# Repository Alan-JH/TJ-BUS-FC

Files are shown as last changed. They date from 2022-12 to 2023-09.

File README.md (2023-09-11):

# Piridium Hardware
Piridium is a CubeSat bus design inspired by TJREVERB and the concept of Pycubed. It uses a Raspberry Pi Zero as a flight computer and Iridium 9602N modem as a radio. The bus is divided into two boards, with the EPS board including six 18650 battery cells and protection and balancing circuitry, and the avionics board including everything else (flight computer, radio, telemetry ADC, inhibits and RBF, solar input charge regulators, 5V output regulator, inertial measurement unit, real time clock and CR2032 battery backup, and payload connector).

## Issues
Charge balance for current EPS prototype seems to not work, despite following datasheet recommendations exactly. Possibly a bad chip, but worth noting.

## Tech Specs
Flight Computer: Raspberry Pi Zero/Zero W

Radio: Iridium 9602N Short Burst Data

Clock: DS3232M RTC with CR2032 Battery Backup

Battery: Six 18650 Li-Ion cells (builder's discretion, recommend protected 3-4Ah) in a 3P2S configuration

Battery protection: ~7.7A overcurrent protection (charge & discharge), 4.29V/cell overcharge protection with hysteresis down to 4.05V/cell, 3V/cell overdischarge protection with hysteresis up to 3.2V/cell

Solar input: 4 input connectors feeding two regulators with 25V Max (limited by the voltage divider for telemetry) with charge cutoff at 8.27V, MPPT settable using a trim pot

Output regulation: 2 separated 5V rails up to 3A output, one for the radio, the other for the Raspberry Pi, each with latching current limiters and a watchdog timer

Payload connection: 1x SPI bus with one dedicated chip enable pin, 1x I2C bus, 1x unused configurable GPIO pin, switchable battery power (no overcurrent protection); see schematic for pinout

Telemetry: Current out and voltage in for both solar regulators, battery input voltage and current, payload battery current

Antenna connector: Standard SMA vertical

Inhibits: Two discharge inhibits (do not block charge), two RBF (one low side ground disconnect, one high side power disconnect, blocks both charge and discharge)

## Hardware notes

### Flight Computer
Raspberry Pi Zero running Raspbian OS lite. Flight software can be found here: https://github.com/Alan-JH/piridium-fsw

### Iridium Modem
Defaults to off when the bus is powered, only turns on when S_MODEM_ON_OFF is pulled high by the Raspberry Pi on GPIO pin 20. There is an LED to indicate when the modem is powered, and GPIO input for ring indicator and network availability (S_RING_INDICATOR on GPIO pin 16 and S_NET_AVAIL on GPIO pin 12, respectively). Communication with the device is done through 3.3V UART, connected to the single UART bus on the Raspberry Pi. There is also a separate connector on the board to be used with a USB to UART converter in case configuration is needed without access to the Raspberry Pi. Due to its strict power requirements the modem can only be powered with the avionics board's 5V regulators, and not through the extra port. All UART connections driven by the Pi run through a 74HC126 buffer to the modem, to prevent latchup conditions if the modem is powered off. A separate patch antenna is required, and can connect with the SMA connector on the board.

### Power Input
There are two LT3652 MPPT tracking charge regulators on the board, each with two input connectors in parallel. The intent is for two solar panels on opposite sides of the CubeSat to be connected to the input of the same regulator, since one will not be producing power while the other is. Input voltage can range up to 25V, and the maximum power point can be set using the trim potentiometer on each regulator. I recommend doing this by connecting a power supply to the input connector, setting its voltage to the desired maximum power point voltage (Vmpp) and adjusting the trim pot until the voltage at the Vmpp test point is 2.7V. The regulators each output up to 2A, and cut off charge at 8.27V float and 0.2A termination. 

### 5V Regulator
There is one TPS54394RSAR regulator on board which outputs two isolated 3A buses, which are configured to 5V. One (labelled 5VP in the schematic) feeds the radio and must not be shared with anything else. The other (labelled 5V in the schematic) feeds the RPi and may be shared, although there is no connector native to the board to do this (and it isn't recommended to share it anyways, as the RPi is an important component). Each rail has its own 5V latching current limiter that disconnects its respective voltage bus in case of an short circuit or overcurrent event on the bus. The current limiter resets after approximately 5 seconds (timed by a simple RC circuit) to check if the overcurrent state has been removed. 

### Watchdog Timer
There is a MAX6369 watchdog timer connected to the enable pin of the 5V regulator, set to reset both 5V buses if a watchdog reset signal is not received for 60 seconds. This watchdog timer is enabled by placing (or soldering) a jumper on the WDT_EN jumper, otherwise it will be disconnected from the enable pin and cannot reset power. The watchdog timer can be disabled for testing but should be enabled for flight as it reboots the system in case of a software crash. The flight software must pulse the watchdog reset pin at least once every 60 seconds if the jumper is in place (including within 60 seconds after starting to boot).

### Telemetry
One MCP3208 ADC provides voltage and current readouts, along with a MAX6035 3V reference. Telemetry readouts include Solar Regulator A Output Current (CH0) and Input Voltage (CH1), Solar Regulator B Output Current (CH2) and Input Voltage (CH3), Battery Voltage (CH4), Battery Output Current (CH5, does not read charging current, only discharging current. Includes payload current), Payload Current draw (CH6). The ADC is on CE0 of the Raspberry Pi. Each telemetry readout has a multiplier which can be found in the flight software example or by doing the math yourself :)

### Real Time Clock
A DS3232M RTC provides an uninterrupted time reading with a CR2032 battery backup. This is located on the I2C1 bus and the Raspberry Pi can be configured to use this RTC for its operating system time. 

### Inertial Measurement Unit
An Adafruit BNO055 may be placed on the board. Honestly, this doesn't really have much use though, as calibration is impossible without moving the board around yourself and gets reset with power cycles.

### Inhibits & RBF
Two inhibits and two RBF pins are available. The two inhibits are placed after the charge output but before the battery output bus on the board, so when enabled they block discharging but not charging. One RBF pin is on the high side between the EPS input terminal and everything else on the board, and the other is on the low side. Both will block discharging and charging when enabled. The inhibit connector is an 8 pin header on the bottom of the board labelled on the silkscreen. Connecting the H and L pins enable the inhibit/RBF, blocking current flow. These should be connected to separation switches on the frame that are closed when depressed. Be careful not to connect the H and L pins of different inhibit/RBFs (e.g. connecting pins 2 and 3).

### Battery protections and balancing
A BQ29209 provides resistive charge balancing and an R5460N212AF provides pack level overcurrent, overvoltage, and undervoltage protections. Due to the 20mOhm resistor connected to the R5460N212AF, battery pack output voltage will droop significantly at higher current draws (e.g. more than a few amps). Overcurrent protection uses the Rds(on) of the two MOSFETs along with the shunt resistor to total 26mOhm, so if the MOSFETs need to be substituted, recalculate the effective series resistance again to see if the resulting OCP setpoint is acceptable. If not, adjust the shunt resistor accordingly. 

## Component selection notes
For passives and unspecified components, select automotive grade (AEC-Q100, AEC-Q101, AEC-Q200, AEC-Q300 etc.) if possible. For capacitors especially, derate voltage by about 50% (i.e. for a capacitor on a line experiencing 5V, choose a cap rated for at least 10V). Also recommend sticking to X7R dielectric and resin body or soft body if possible. For 0.1uF caps, 50V for everything is fine. For 10uF, I had to order a bunch of 25V automotive grade caps for everything and a few 50V non automotive caps specifically for the solar input. For current shunts, derate the power rating by a similar amount for thermal concerns.

For the CR2032 battery, I used a Murata CR2032W for its +125C max operating temperature. The battery holder is a LINX-HLD-001-THM. For the battery terminals, use Phoenix Contact 1985807

Shield: [][cc-by-nc-sa]

This work is licensed under a
[Creative Commons Attribution-NonCommercial-ShareAlike 4.0 International License][cc-by-nc-sa].

[][cc-by-nc-sa]

[cc-by-nc-sa]: http://creativecommons.org/licenses/by-nc-sa/4.0/
[cc-by-nc-sa-image]: https://licensebuttons.net/l/by-nc-sa/4.0/88x31.png
[cc-by-nc-sa-shield]: https://img.shields.io/badge/License-CC%20BY--NC--SA%204.0-lightgrey.svg

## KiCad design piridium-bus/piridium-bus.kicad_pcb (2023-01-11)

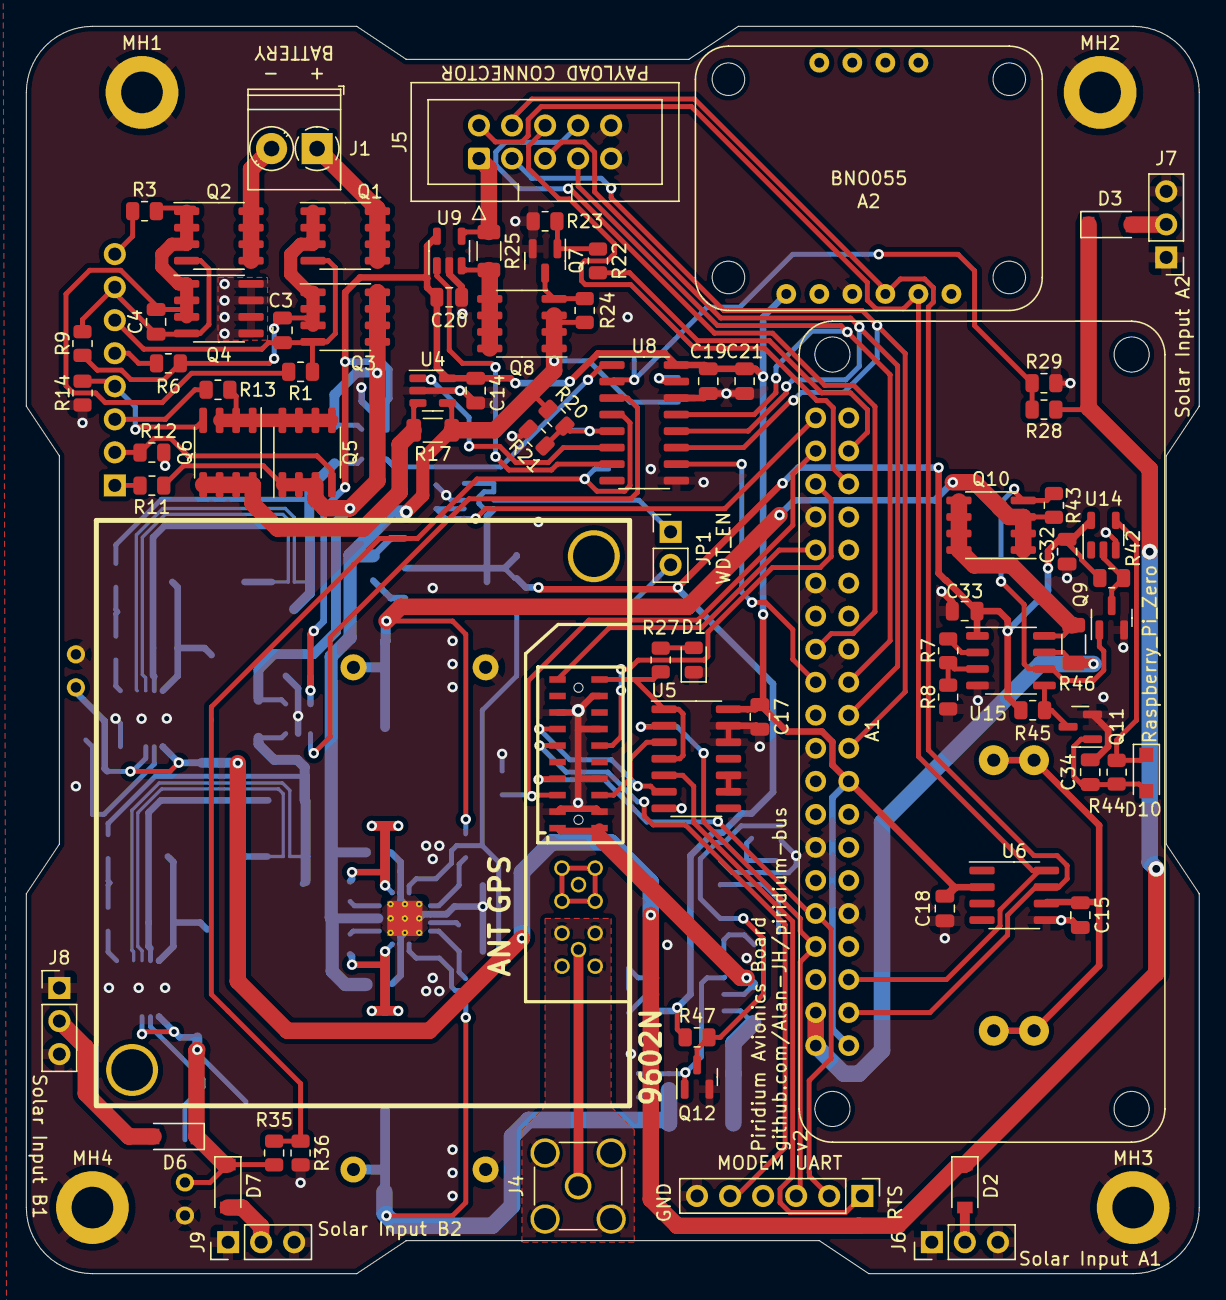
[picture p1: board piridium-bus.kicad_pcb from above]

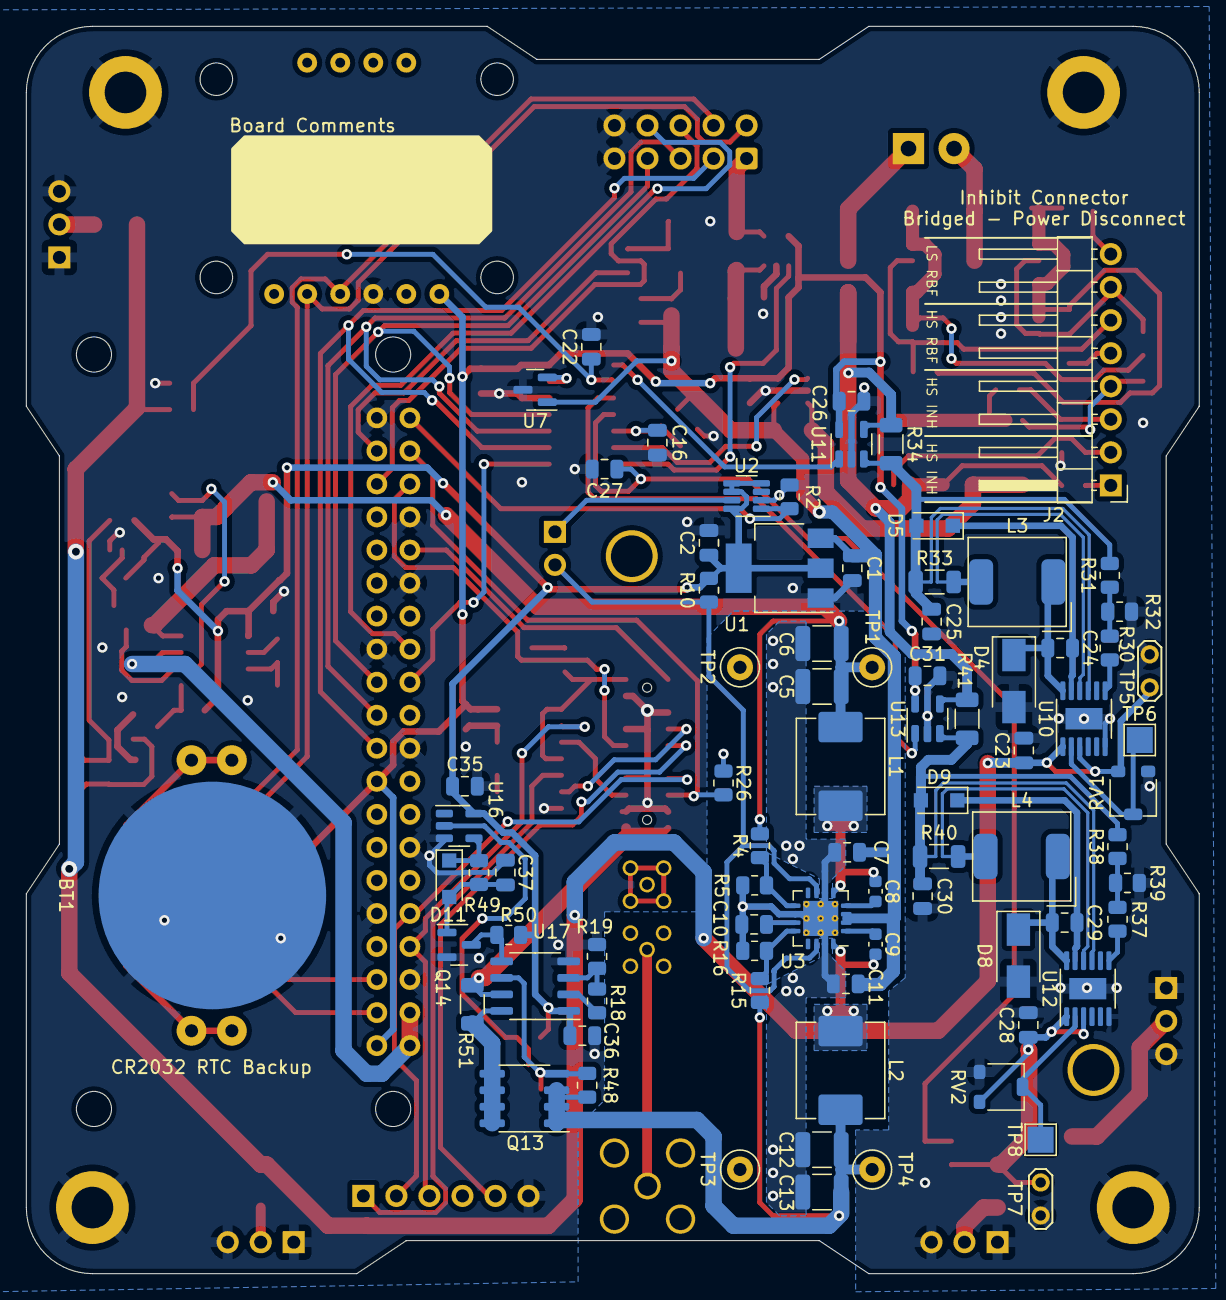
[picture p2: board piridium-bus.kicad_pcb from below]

Board: 4 copper layers, 90.2 x 95.9 mm, 162 parts (81 on the bottom side), 104 nets.

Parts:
A1: Raspberry_Pi_Zero; Raspberry Pi Zero
A2: BNO055
A3: 9602N; 9602
BT1: CR2032; CR2032-LINX-HLD-001-THM
C1, C7, C11, C21, C23, C25, C28, C30, C34, C37: 10uF; C_0805_2012Metric
C2, C3, C4, C14, C16, C17, C19, C20, C22, C26, C27, C31, C32, C33, C35, C36: 0.1uF; C_0805_2012Metric
C5, C6, C12, C13: 22uF; C_1210_3225Metric
C8, C9: 0.1uF; C_0603_1608Metric
C10, C15, C18, C24, C29: 1uF; C_0805_2012Metric
D1: LED; LED_0805_2012Metric
D2, D3, D6, D7: DFLS130L-7; D_SOD-123
D4, D8: CMSH3-40MA; D_SMA
D5, D9, D10, D11: RB051MM-2Y; D_SOD-123F
J1: EPS; TerminalBlock_Phoenix_PT-1,5-2-3.5-H_1x02_P3.50mm_Horizontal
J2: INHIBITS; PinHeader_1x08_P2.54mm_Horizontal
J3: MODEM UART; PinHeader_1x06_P2.54mm_Vertical
J4: ANT; SMA_Amphenol_901-144_Vertical
J5: PAYLOAD; IDC-Header_2x05_P2.54mm_Vertical
J6, J8: IN1; PinHeader_1x03_P2.54mm_Vertical
J7, J9: IN2; PinHeader_1x03_P2.54mm_Vertical
JP1: WDT_EN; PinHeader_1x02_P2.54mm_Vertical
L1, L2: 4.7uH; L_Abracon_ASPI-0630LR
L3, L4: 10uH; L_AVX_LMLP07A7
MH1, MH2, MH3, MH4: M3; MountingHole_3.2mm_M3_DIN965_Pad
Q1, Q3, Q5, Q6, Q8, Q10, Q13: DMP3015LSSQ; SOIC-8_3.9x4.9mm_P1.27mm
Q2, Q4: Si4186DY; SOIC-8_3.9x4.9mm_P1.27mm
Q7, Q9, Q11, Q12, Q14: 2N7002; SOT-23
R1, R2, R9, R10, R12, R14, R21: 100K; R_0805_2012Metric
R3, R6, R11, R13, R22: 100R; R_0805_2012Metric
R4, R15: 124K; R_0805_2012Metric
R5, R16: 22.1K; R_0805_2012Metric
R7, R18: 6K; R_0805_2012Metric
R8, R19: 4K; R_0805_2012Metric
R17, R25, R34, R41: 4m; R_1206_3216Metric
R20: 200K; R_0805_2012Metric
R23, R24, R26, R27, R29, R36, R42, R43, R45, R47, R48, R50: 10K; R_0805_2012Metric
R28, R35: 75K; R_0805_2012Metric
R30, R37: 191K; R_0805_2012Metric
R31, R38: 147K; R_0805_2012Metric
R32, R39: 97.6K; R_0805_2012Metric
R33, R40: 50m; R_1206_3216Metric
R44, R49: 510K; R_0805_2012Metric
R46, R51: 10m; R_1206_3216Metric
RV1, RV2: 100K; Bourns PVG3A
TP1: 5V; TestPoint_Loop_D2.50mm_Drill1.0mm
TP2, TP3: GND; TestPoint_Loop_D2.50mm_Drill1.0mm
TP4: 5VP; TestPoint_Loop_D2.50mm_Drill1.0mm
TP5, TP7: VIN; TestPoint_2Pads_Pitch2.54mm_Drill0.8mm
TP6, TP8: Vmpp; TestPoint_Pad_2.0x2.0mm
U1: LM1117-3.3; SOT-223-3_TabPin2
U2: MAX6369; SOT-23-8
U3: TPS54394RSAR; Texas_S-PVQFN-N16_EP2.7x2.7mm_ThermalVias
U4, U9, U11, U13: INA180A3; SOT-23-5
U5: 74HC126; SOIC-14_3.9x8.7mm_P1.27mm
U6: DS3232M; SOIC-8_3.9x4.9mm_P1.27mm
U7: MAX6035xxUR30; SOT-23
U8: MCP3208; SOIC-16_3.9x9.9mm_P1.27mm
U10, U12: LT3652EMSE; MSOP-12-1EP_3x4mm_P0.65mm_EP1.65x2.85mm
U14, U16: SN74LVC1G14DBV; SOT-23-5
U15, U17: MAX4373F; SO-8_3.9x4.9mm_P1.27mm

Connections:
+3.3V: A1.1 (3V3), A1.17 (3V3), A2.1 (VIN), C14.1, C17.1, C18.2, C19.1, C20.1, C21.1, C26.1, C31.1, U4.5 (V+), U5.14 (VCC), U6.2 (VCC), U8.16 (Vdd), U9.5 (V+), U11.5 (V+), U13.5 (V+)
+3.3VA: C2.1, C32.1, C33.1, C35.1, C36.1, R10.1, R42.1, R45.1, R47.1, R50.1, U1.2 (VO), U2.4 (SET0), U2.5 (SET1), U2.6 (SET2), U2.8 (VCC), U14.5 (VCC), U15.1 (Vcc), U16.5 (VCC), U17.1 (Vcc)
+5V: A1.2 (5V), A1.4 (5V), R46.1, U15.7 (RS-)
+5VP: A3.1 (EXT_PWR), A3.2 (EXT_PWR), R51.1, U17.7 (RS-)
+BATT: C1.1, C7.1, C11.1, Q8.1 (S), Q8.2 (S), Q8.3 (S), R17.1, R20.1, R24.1, U1.3 (VI), U3.2 (VIN2), U3.3 (VIN1), U4.4 (-), U7.1 (IN)
/5V LCL/CIN1: R7.2, R8.1, U15.3 (CIN1)
/5V LCL/OUT: R7.1, U15.2 (OUT)
/5V LCL/POWER_IN: C5.1, C6.1, L1.1, Q10.1 (S), Q10.2 (S), Q10.3 (S), R4.1, R43.1, TP1.1
/5VP LCL/CIN1: R18.2, R19.1, U17.3 (CIN1)
/5VP LCL/OUT: R18.1, U17.2 (OUT)
/5VP LCL/POWER_IN: C12.1, C13.1, L2.2, Q13.1 (S), Q13.2 (S), Q13.3 (S), R15.1, R48.1, TP4.1
/A1H: J2.5, R6.2
/A1L: C3.2, J2.6, Q1.4 (G), Q3.4 (G), R1.1
/A2H: C4.1, J2.7, Q2.4 (G), Q4.4 (G), R9.2
/A2L: J2.8, R3.1
/B1H: J2.1, R11.2
/B1L: J2.2, Q5.4 (G), R12.1
/B2H: J2.3, R13.2
/B2L: J2.4, Q6.4 (G), R14.1
/CHARGE_OUT: Q3.5 (D), Q3.6 (D), Q3.7 (D), Q3.8 (D), Q5.1 (S), Q5.2 (S), Q5.3 (S), R11.1, R34.1, R41.1, U11.4 (-), U13.4 (-)
/EN: JP1.2 (B), R10.2, U3.7 (EN1), U3.14 (EN2)
/I_OUT_A: U8.1 (CH0), U11.1
/I_OUT_B: U8.3 (CH2), U13.1
/PAYLOAD_PWR: J5.1, R25.1, U9.4 (-)
/SUP_OUT: A3.20 (SUPPLY_OUT), R27.1, U5.1, U5.4
/V_IN_A: C22.1, R28.2, R29.1, U8.2 (CH1)
/V_IN_B: C27.1, R35.2, R36.1, U8.4 (CH3)
ADC_CS: A1.24 (8(CE0)), U8.10 (~CS/SHDN)
GND: A1.6 (GND), A1.9 (GND), A1.14 (GND), A1.20 (GND), A1.25 (GND), A1.30 (GND), A1.34 (GND), A1.39 (GND), A2.3 (GND), A3.3 (EXT_GND), A3.4 (EXT_GND), A3.8 (SIG_GND), A3.14 (DF_DTR), A3.15 (SIG_GND), A3.18 (SIG_GND), BT1.2 (-), C1.2, C2.2, C5.2, C6.2, C7.2, C10.2, C11.2, C12.2, C13.2, C14.2, C15.2, C16.2, C17.2, C18.1, C19.2, C20.2, C21.2, C22.2, C23.2, C25.2, C26.2, C27.2, C28.2, C30.2, C31.2, C32.2, C33.2, C34.2, C35.2, C36.2, C37.2, D1.1 (K), D4.2 (A), D8.2 (A), J3.6, J5.9, J5.10, J6.1, J6.3, J7.1, J7.3, J8.1, J8.3, J9.1, J9.3, MH1.1, MH2.1, MH3.1, MH4.1, Q4.5 (D), Q4.6 (D), Q4.7 (D), Q4.8 (D), Q7.2 (S), Q9.2 (S), Q11.2 (S), Q12.2 (S), Q14.2 (S), R2.2, R5.2, R8.2, R12.2, R14.2, R16.2, R19.2, R21.2, R23.2, R26.2, R29.2, R32.1, R36.2, R39.1, RV1.3, RV2.3, TP2.1, TP3.1, TP5.1, TP7.1, U1.1 (GND), U2.2 (GND), U3.6 (PGND1), U3.10 (GND), U3.15 (PGND2), U3.17 (PADGND), U4.2 (GND), U5.7 (GND), U5.9, U5.10, U5.12, U5.13, U6.5 (GND), U7.3 (GND), U8.9 (DGND), U8.14 (AGND), U9.2 (GND), U10.6 (TIMER), U10.13 (GND), U11.2 (GND), U12.6 (TIMER), U12.13 (GND), U13.2 (GND), U14.3 (GND), U15.4 (GND), U16.3 (GND), U17.4 (GND)
GNDS: A3.22 (RF_GND), J4.2 (Ext)
GPIO19: A1.35 (19(PWM1)), J5.6
I2C_SCL: A1.5 (3(SCL1)), A2.5 (SCL), J5.2, U6.8 (SCL)
I2C_SDA: A1.3 (2(SDA1)), A2.4 (SDA), J5.4, U6.7 (SDA)
unnamed: A3.6 (DF_S_TX), U5.3
unnamed: A3.13 (DF_RTS), U5.6
unnamed: A3.21 (RF_ANT), J4.1 (In)
unnamed: BT1.1 (+), C15.1, U6.6 (VBAT)
unnamed: C3.1, Q1.1 (S), Q1.2 (S), Q1.3 (S), Q3.1 (S), Q3.2 (S), Q3.3 (S), R6.1, R9.1
unnamed: C4.2, Q2.1 (S), Q2.2 (S), Q2.3 (S), Q4.1 (S), Q4.2 (S), Q4.3 (S), R1.2, R3.2
unnamed: C8.1, U3.4 (VBST1)
unnamed: C8.2, L1.2, U3.5 (SW1)
unnamed: C9.1, U3.1 (VBST2)
unnamed: C9.2, L2.1, U3.16 (SW2)
unnamed: C10.1, U3.11 (VREG5)
unnamed: C23.1, D2.1 (K), D3.1 (K), R28.1, RV1.1, TP5.2, U10.1 (VIN), U10.3 (~SHDN)
unnamed: C24.1, D4.1 (K), L3.1, U10.12 (SW)
unnamed: C24.2, D5.1 (K), U10.11 (BOOST)
unnamed: C25.1, D5.2 (A), R31.2, R33.1, R34.2, U10.9 (BAT), U11.3 (+)
unnamed: C28.1, D6.1 (K), D7.1 (K), R35.1, RV2.1, TP7.2, U12.1 (VIN), U12.3 (~SHDN)
unnamed: C29.1, D8.1 (K), L4.1, U12.12 (SW)
unnamed: C29.2, D9.1 (K), U12.11 (BOOST)
unnamed: C30.1, D9.2 (A), R38.2, R40.1, R41.2, U12.9 (BAT), U13.3 (+)
unnamed: C34.1, D10.2 (A), Q11.1 (G), R44.2
unnamed: C37.1, D11.2 (A), Q14.1 (G), R49.2
unnamed: D1.2 (A), R27.2
unnamed: D2.2 (A), J6.2
unnamed: D3.2 (A), J7.2
unnamed: D6.2 (A), J8.2
unnamed: D7.2 (A), J9.2
unnamed: D10.1 (K), R44.1, U14.4
unnamed: D11.1 (K), R49.1, U16.4
unnamed: J1.1, Q1.5 (D), Q1.6 (D), Q1.7 (D), Q1.8 (D)
unnamed: J1.2, Q2.5 (D), Q2.6 (D), Q2.7 (D), Q2.8 (D)
unnamed: JP1.1 (A), U2.7 (~WDO)
unnamed: L3.2, R33.2, U10.10 (SENSE)
unnamed: L4.2, R40.2, U12.10 (SENSE)
unnamed: Q5.5 (D), Q5.6 (D), Q5.7 (D), Q5.8 (D), Q6.1 (S), Q6.2 (S), Q6.3 (S), R13.1
unnamed: Q6.5 (D), Q6.6 (D), Q6.7 (D), Q6.8 (D), R17.2, U4.3 (+)
unnamed: Q7.1 (G), R22.1, R23.1
unnamed: Q7.3 (D), Q8.4 (G), R24.2
unnamed: Q8.5 (D), Q8.6 (D), Q8.7 (D), Q8.8 (D), R25.2, U9.3 (+)
unnamed: Q9.3 (D), R42.2, U14.2
unnamed: Q9.1 (G), Q10.4 (G), R43.2, U15.6 (COUT1)
unnamed: Q10.5 (D), Q10.6 (D), Q10.7 (D), Q10.8 (D), R46.2, U15.8 (RS+)
unnamed: Q11.3 (D), R45.2, U15.5 (~RESET)
unnamed: Q12.1 (G), Q13.4 (G), R48.2, U17.6 (COUT1)
unnamed: Q12.3 (D), R47.2, U16.2
unnamed: Q13.5 (D), Q13.6 (D), Q13.7 (D), Q13.8 (D), R51.2, U17.8 (RS+)
unnamed: Q14.3 (D), R50.2, U17.5 (~RESET)
unnamed: R4.2, R5.1, U3.9 (VFB1)
unnamed: R15.2, R16.1, U3.12 (VFB2)
unnamed: R30.1, R31.1, R32.2
unnamed: R30.2, U10.7 (VFB)
unnamed: R37.1, R38.1, R39.2
unnamed: R37.2, U12.7 (VFB)
unnamed: RV1.2, TP6.1, U10.2 (VIN_REG)
unnamed: RV2.2, TP8.1, U12.2 (VIN_REG)
unnamed: U7.2 (OUT), U8.15 (Vref)
SPI_CE1: A1.26 (7(CE1)), J5.8
SPI_MISO: A1.21 (9(MISO)), J5.5, U8.12 (Dout)
SPI_MOSI: A1.19 (10(MOSI)), J5.3, U8.11 (Din)
SPI_SCK: A1.23 (11(SCK)), J5.7, U8.13 (CLK)
S_HANDSHAKE: A1.40 (21), R2.1, U2.1 (WDI)
S_MODEM_ON_OFF: A1.38 (20), A3.5 (ON/OFF), R26.1
S_NET_AVAIL: A1.32 (12(PWM0)), A3.19 (NET_AVAIL)
S_PAYLOAD_PWR: A1.37 (26), R22.2
S_RING_INDICATOR: A1.36 (16), A3.12 (DF_RI)
TELEM_IBAT: U4.1, U8.6 (CH5)
TELEM_IPAYLOAD: U8.7 (CH6), U9.1
TELEM_VBATV: C16.1, R20.2, R21.1, U8.5 (CH4)
UART_CTS: A3.11 (DF_CTS), J3.5
UART_RTS: J3.1, U5.5
UART_RX: A1.10 (15(RxD)), A3.7 (DF_S_RX), J3.2
UART_TX: A1.8 (14(TxD)), J3.3, U5.2

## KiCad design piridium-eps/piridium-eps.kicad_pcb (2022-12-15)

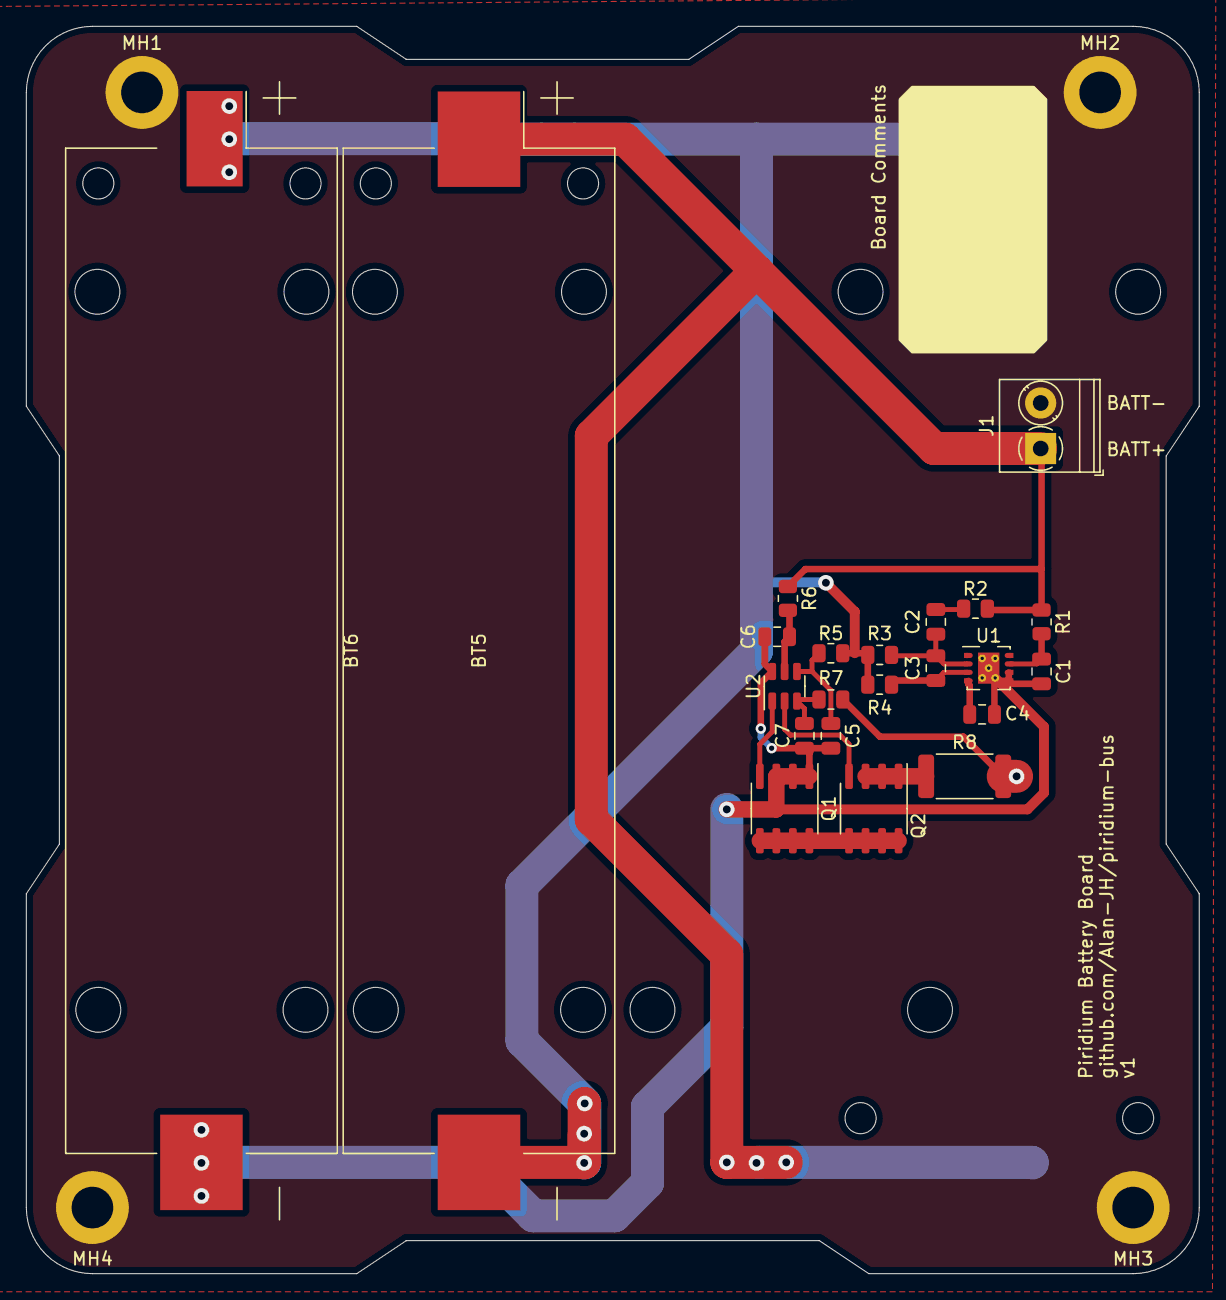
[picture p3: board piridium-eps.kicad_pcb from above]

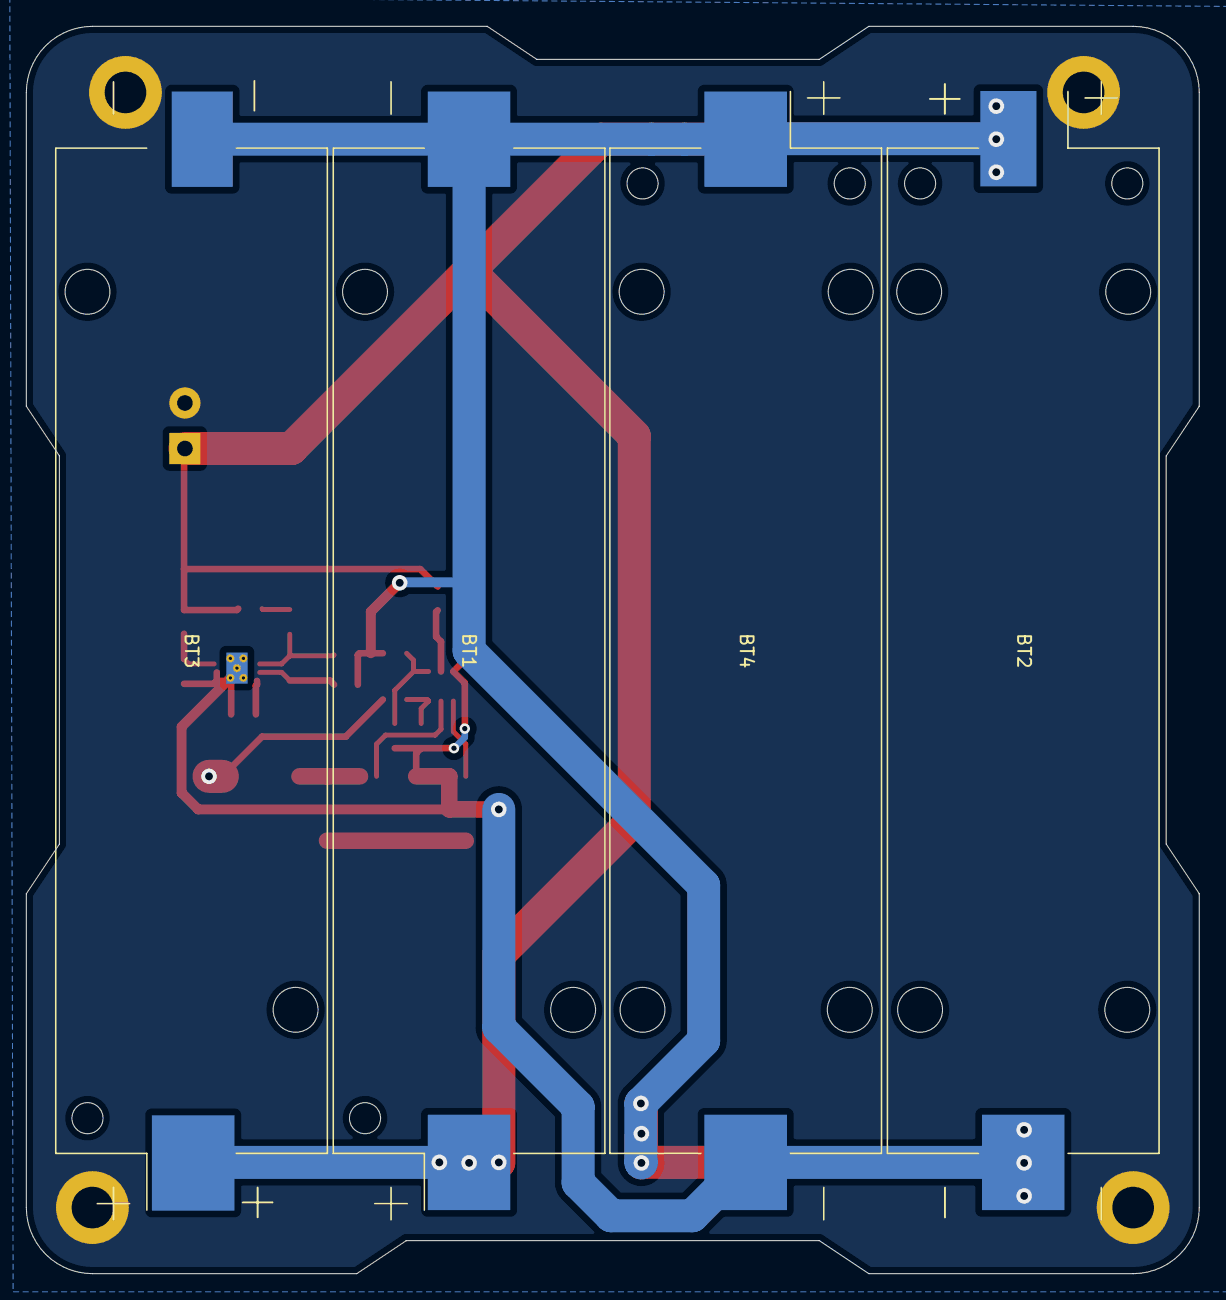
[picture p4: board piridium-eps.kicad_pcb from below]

Board: 2 copper layers, 90.2 x 95.9 mm, 30 parts (4 on the bottom side), 16 nets.

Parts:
BT1, BT4, BT5: 18650; BatteryHolder_Keystone_1042_1x18650
BT2: 18650; Keystone_1042_1x18650_Shortpad
BT3: 18650; Keystone_1042_1x18650_Shortpad2
BT6: 18650; Keystone_1042_1x18650_Shortpad3
C1, C2, C3, C4, C5, C6, C7: 0.1uF; C_0805_2012Metric
J1: EPS; TerminalBlock_Phoenix_PT-1,5-2-3.5-H_1x02_P3.50mm_Horizontal
MH1, MH2, MH3, MH4: M3; MountingHole_3.2mm_M3_DIN965_Pad
Q1, Q2: Si4186DY; SOIC-8_3.9x4.9mm_P1.27mm
R1, R4: 100R; R_0805_2012Metric
R2: 160R; R_0805_2012Metric
R3, R5, R6: 261R; R_0805_2012Metric
R7: 1K; R_0805_2012Metric
R8: 20m; R_2512_6332Metric
U1: BQ29209; Texas_S-PVSON-N8_ThermalVias
U2: R5460N212AF; SOT-23-6

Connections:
+BATT: BT1.1 (+), BT3.1 (+), BT5.1 (+), J1.1, R1.1, R2.1, R6.1
-BATT: BT2.2 (-), BT4.2 (-), BT6.2 (-), C1.2, C4.2, C5.2, C6.2, C7.1, Q1.1 (S), Q1.2 (S), Q1.3 (S), U1.5 (GND), U1.6 (~{CB_EN), U1.9 (PGND), U2.6 (Vss)
GND: J1.2, MH1.1, MH2.1, MH3.1, MH4.1, R7.2, R8.2
unnamed: BT1.2 (-), BT2.1 (+), BT3.2 (-), BT4.1 (+), BT5.2 (-), BT6.1 (+), R3.1, R4.1, R5.1
unnamed: C1.1, R1.2, U1.7 (VDD)
unnamed: C2.1, R2.2
unnamed: C2.2, C3.1, R3.2, U1.2 (VC1)
unnamed: C3.2, R4.2, U1.3 (VC1_CB)
unnamed: C4.1, U1.4 (CD)
unnamed: C5.1, R5.2, U2.4 (Vc)
unnamed: C6.1, R6.2, U2.5 (Vdd)
unnamed: C7.2, R7.1, U2.3 (V-)
unnamed: Q1.4 (G), U2.1 (Dout)
unnamed: Q1.5 (D), Q1.6 (D), Q1.7 (D), Q1.8 (D), Q2.5 (D), Q2.6 (D), Q2.7 (D), Q2.8 (D)
unnamed: Q2.1 (S), Q2.2 (S), Q2.3 (S), R8.1
unnamed: Q2.4 (G), U2.2 (Cout)

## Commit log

2022-03-28 add iridium-stack components
    [TJ-BUS-FC.kicad_pcb, TJ-BUS-FC.kicad_sch]
2022-03-28 teensy lib
    [Iridium.kicad_sch, TJ-BUS-FC.kicad_sch]
2022-04-02 minor fix
    [TJ-BUS-FC.kicad_sch]
2022-10-18 fresh start
    [piridium-bus.kicad_pcb, piridium-bus.kicad_sch]
2022-10-20 sch milestone
    [piridium-bus.kicad_sch]
2022-10-25 finish up piridium-bus schematic, cleanup footprint associations and symbols, start battery
    [Iridium.kicad_sch, TJ-BUS-FC.kicad_pcb, TJ-BUS-FC.kicad_sch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]
2022-10-25 transfer some TJ-EPS circuitry to eps
    [piridium-eps.kicad_sch]
2022-10-31 some work on routing
    [piridium-bus.kicad_pcb, piridium-bus.kicad_sch]
2022-11-01 routing work on bus
    [piridium-bus.kicad_pcb, piridium-bus.kicad_sch]
2022-11-02 update routing
    [piridium-bus.kicad_pcb, piridium-bus.kicad_sch]
2022-11-05 add inhibits, telemetry, and solar to bus
    [Solar.kicad_sch, piridium-bus.kicad_pcb, piridium-bus.kicad_sch]
2022-11-06 fix bus board messup, remove redundant components from eps
    [piridium-bus.kicad_pcb, piridium-bus.kicad_sch, piridium-eps.kicad_sch]
2022-11-10 ngl not sure what I did here
    [piridium-bus.kicad_pcb, piridium-bus.kicad_sch]
2022-11-10 routing work
    [piridium-bus.kicad_pcb]
2022-11-16 route inhibits and some other power path stuff
    [piridium-bus.kicad_pcb, piridium-bus.kicad_sch]
2022-11-17 route data lines, begin to route MPPT circuitry
    [Solar.kicad_sch, piridium-bus.kicad_pcb, piridium-bus.kicad_sch]
2022-11-17 route solar
    [piridium-bus.kicad_pcb]
2022-11-17 finish routing
    [piridium-bus.kicad_pcb]
2022-11-17 cleanup silkscreen
    [piridium-bus.kicad_pcb]
2022-11-17 copy pycubed battery
    [piridium-eps.kicad_sch]
2022-11-21 add max4373f
    [piridium-bus.kicad_sch]
2022-11-28 prototype timing circuit for LCL reset
    [Solar.kicad_sch, piridium-bus.kicad_sch]
2022-11-28 move LCLs to hierarchical sheets
    [LCL.kicad_sch, piridium-bus.kicad_sch]
2022-11-29 add R5460 and small bom edits
    [LCL.kicad_sch, piridium-bus.kicad_sch, piridium-eps.kicad_sch]
2022-11-29 battery sch finish
    [LCL.kicad_sch, Solar.kicad_sch, piridium-bus.kicad_pcb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]
2022-12-01 route LCLs
    [piridium-bus.kicad_pcb]
2022-12-13 finish battery
    [piridium-eps-B_Cu.gbr, piridium-eps-B_Mask.gbr, piridium-eps-B_Paste.gbr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]
2022-12-15 switch battery to 2 layer
    [piridium-eps-B_Cu.gbr, piridium-eps-B_Mask.gbr, piridium-eps-B_Paste.gbr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]
2022-12-19 correct max4373 implementation, #5 and #4
    [LCL.kicad_sch, piridium-bus.kicad_pcb, piridium-bus.kicad_sch]
2022-12-22 move adc to hardware cs pin, start routing updated LCLs
    [piridium-bus.kicad_pcb, piridium-bus.kicad_sch]
2022-12-23 finish v2 (#6 and finish #5/#4)
    [piridium-bus-B_Cu.gbr, piridium-bus-B_Mask.gbr, piridium-bus-B_Paste.gbr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]
2022-12-28 mcp3208 constant reference
    [LCL.kicad_sch, Solar.kicad_sch, piridium-bus.kicad_pcb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]
2022-12-28 gerber re export
    [piridium-bus-B_Cu.gbr, piridium-bus-B_Mask.gbr, piridium-bus-B_Paste.gbr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]
2022-12-29 pull down on/off instead of up
    [LCL.kicad_sch, Solar.kicad_sch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]
2022-12-29 final trace edits
    [piridium-bus-B_Cu.gbr, piridium-bus-B_Mask.gbr, piridium-bus-B_Paste.gbr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]
2023-01-11 fix max6035 dropout
    [piridium-bus-B_Cu.gbr, piridium-bus-B_Mask.gbr, piridium-bus-B_Paste.gbr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]

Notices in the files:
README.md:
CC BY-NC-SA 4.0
